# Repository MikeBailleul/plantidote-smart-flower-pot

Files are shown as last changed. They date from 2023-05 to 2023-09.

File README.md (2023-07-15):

# Plantidote - A smart flower pot, self-watering

Plantidote, the antidote to never worry about failing your plants again.

How many times have you found yourself on the brink of dehydration, parched, staring at your glass of water, but too lazy to actually pick it up and sip? Now, imagine that, but you're a plant 🌱. Imagine the thirst. 💦 The despair... 😩

Plantidote will automatically check for moisture level in the planter and will water itself if needed.

# Table of Contents
- [How to build your own](#how-to-build-your-own)
  * [BOM](#bom)
  * [PCB](#pcb)
  * [3D printing](#3d-printing)
- [Build instructions](#build-instructions)
  * [Making the shell water Resistant](#making-the-shell-water-resistant)
  * [Soldering](#soldering)
  * [Assembling the bottom part](#assembling-the-bottom-part)
  * [Assembling the top part](#assembling-the-top-part)
- [Home Assistant & ESPHome Instructions](#home-assistant--esphome-instructions)
- [Blynk Instructions](#blynk-instructions)
- [PCB design choices](#pcb-design-choices)
- [Some Fusion 360 PCB tips](#some-fusion-360-pcb-tips)

# History of the project
Plantidote is based on [this awesome idea](https://github.com/FlauraPlantPot/Flaura) by Martin McMaker.
Unfortunately, it was working only with Blynk and the pot was difficult to make waterproof.

I completely redesigned the PCB and some parts of 3D models.
It is now easier to seal, requiring only 2 seal points. Hot glue or silicone sealant can be used. Thanks to Martin Vinter for [the inspiration](https://github.com/MartinVinter/Flaura2)

This new smart pot works with:
- HomeAssistant/ESPHome. Home Assistant code is derived from MathGaming [modified version of Flaura](https://github.com/mathgaming/FlauraHomeAssistant).  Many thanks to him.
- [Blynk](https://blynk.cloud/)

Plantidote has 4 design variations for the external shell and can be printed in different colors (shell & top lid).

| Round | Knurl | Spin | V Shape |
| --- | --- | --- | --- |
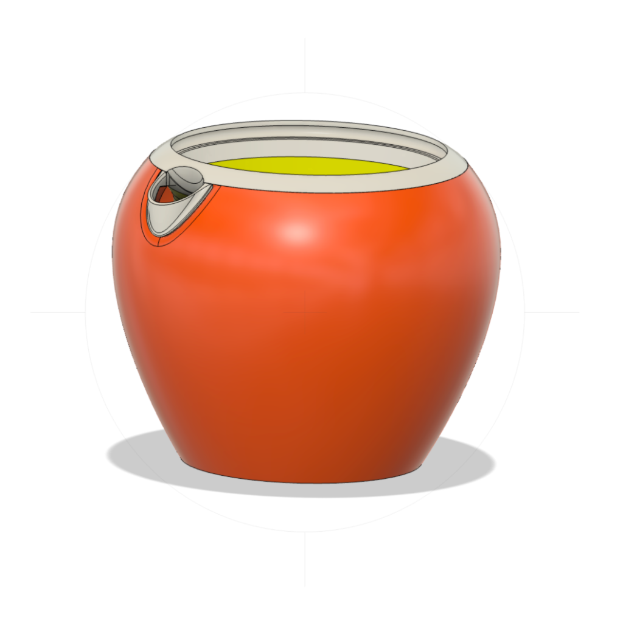
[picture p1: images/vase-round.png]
round
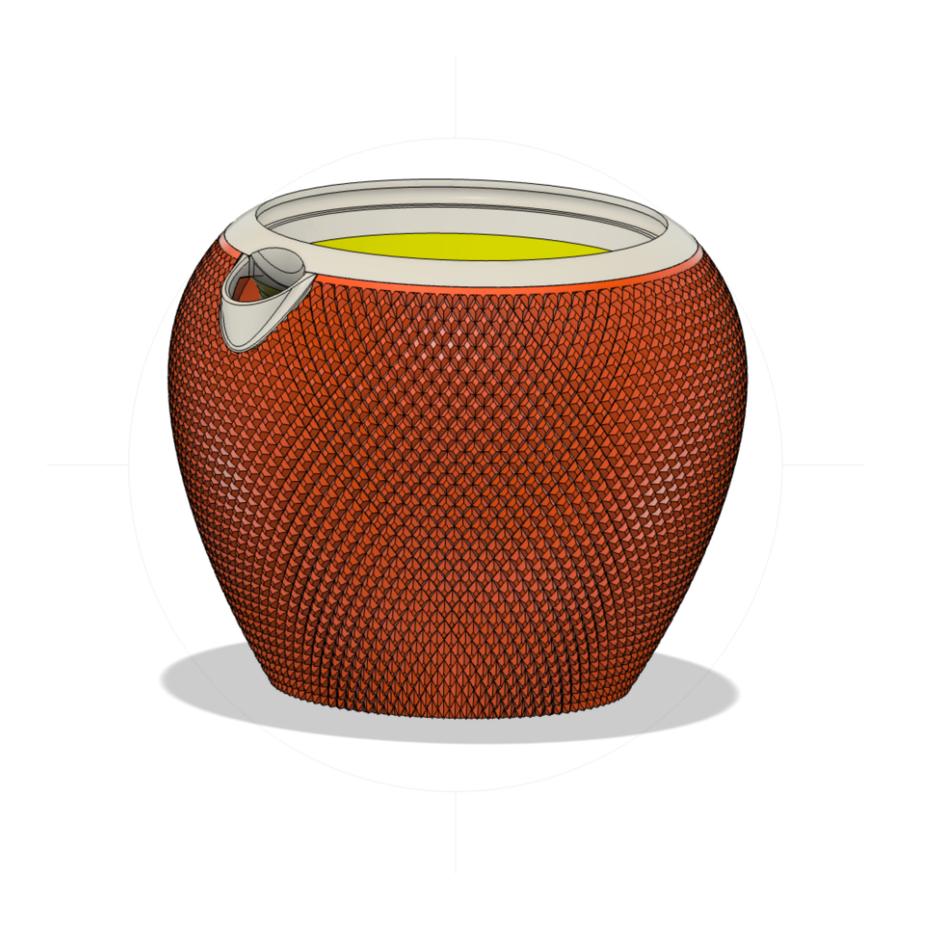
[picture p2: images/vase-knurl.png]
knurl
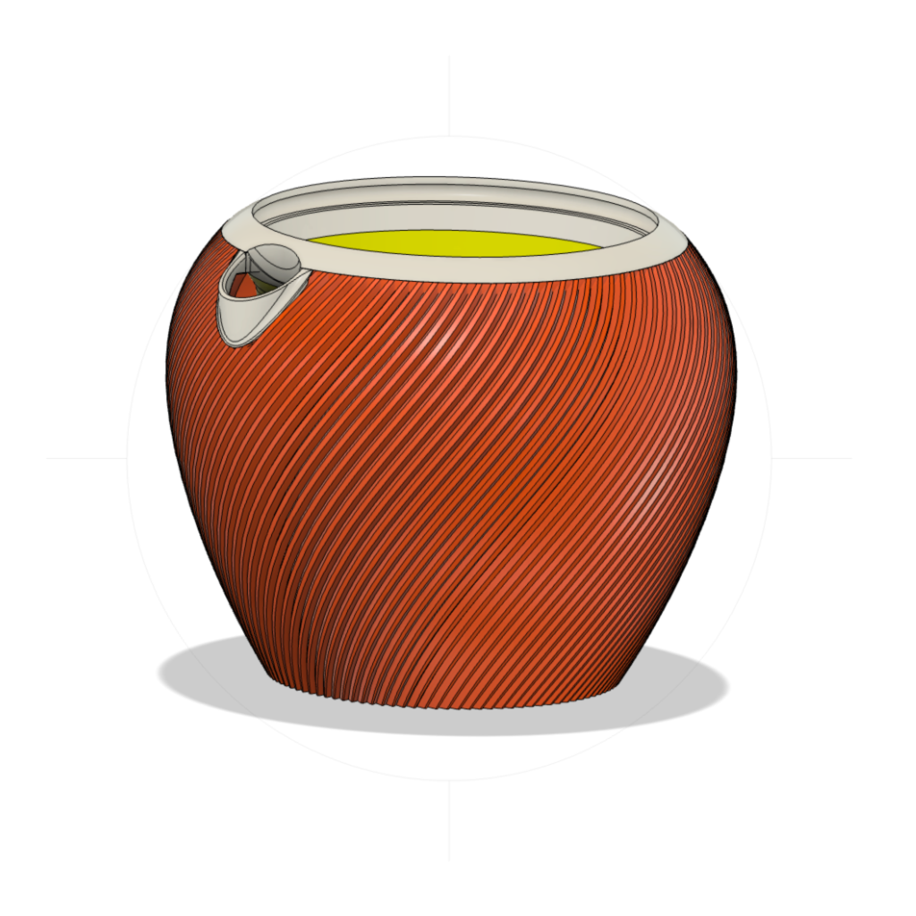
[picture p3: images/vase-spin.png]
spin
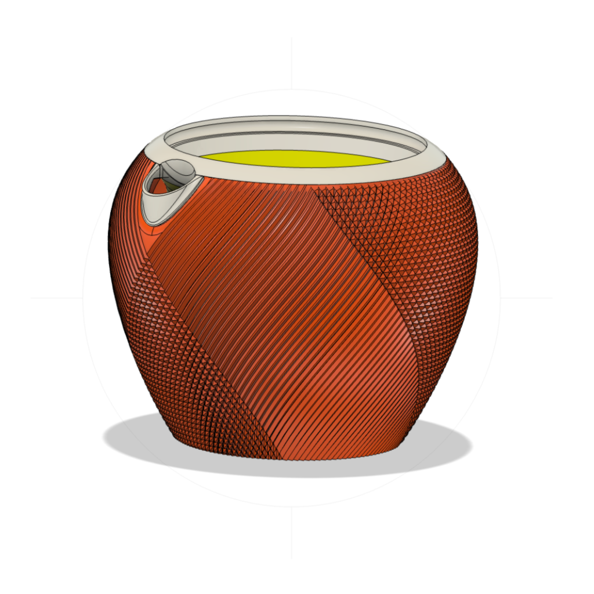
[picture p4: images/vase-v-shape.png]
v shape
|  |  |  |  |

The vase can be autonomous for months thanks to its 0.5L water tank and its battery. The volume of the flower pot is 0.8L.

# How to build your own

## BOM

#### Hoses
| Name | Type | Diameter | Length | Link |
| --- | --- | --- | --- | --- |
| Hose - Watering ring  | PTFE | Ø4-Ø2mm | 365mm | [AliExpress](https://www.aliexpress.com/item/1005001976975889.html) |
| Hose - Ring/T | Silicone | Ø5-Ø3mm | 90mm | [AliExpress](https://www.aliexpress.com/item/1005002185082384.html) |
| Hose - "bridge" T-connector/Pot | Silicone | Ø5-Ø3mm | 2 x 15mm | [AliExpress](https://www.aliexpress.com/item/1005002185082384.html) |
| Hose - Pump | Silicone | Ø5-Ø3mm | 40mm + 50mm | [AliExpress](https://www.aliexpress.com/item/1005002185082384.html) |
| T-connector |  | Ø3.2-Ø2.4mm |  | [AliExpress](https://www.aliexpress.com/item/1005004196182380.html) |

PVC hose could work as well, but I advise silicone instead because it is softer and will prevent you from breaking the 3D printed hose connectors.

#### Electronics
| Quantity | Name | Specs | Note | Link |
| --- | --- | --- | --- | --- |
| 1 | Lolin D32 |  |  | [AliExpress](https://www.aliexpress.com/item/32808551116.html) |
| 1 | Diaphragm water pump | DC 3.7V | 2 visible diaphragms -> suitable for water | [AliExpress](https://www.aliexpress.com/item/4000974989453.html) |
| 3 | Resistor | 100kΩ |  | [AliExpress](https://www.aliexpress.com/item/32636020144.html) |
| 1 | Resistor | 330Ω |  | [AliExpress](https://www.aliexpress.com/item/32636020144.html) |
| 1 | Ceramic capacitor | 100nF |  | [AliExpress](https://www.aliexpress.com/item/1005003563792431.html) |
| 1 | Diode 1N4007 | 1A |  | [AliExpress](https://www.aliexpress.com/item/32633071171.html) |
| 1 | MOSFET IR**L**Z44N | Logic level | Don't confuse with : IR**F**Z44N | [AliExpress](https://www.aliexpress.com/item/32714396199.html) |
| 1 | Push button | 6x6x4.3mm |  | [AliExpress](https://www.aliexpress.com/item/4001223843274.html) |
| 1 | Power switch | SK12D07VG6 (6mm) |  | [AliExpress](https://www.aliexpress.com/item/1005003663462833.html) |
| 2 | Pin Header Female 16 Pins |  | PCB/LolinD32 connectors | [AliExpress](https://www.aliexpress.com/item/33004522737.html) |
| 1 | Pin Header Male 3 Pins |  | PCB/Moisture sensor connectors | [AliExpress](https://www.aliexpress.com/item/32758380907.html) |
| 2 | JST Connector Male/Female 2 Pins | PH Pitch 2.0 | Pump & battery connectors | [AliExpress](https://www.aliexpress.com/item/33009614944.html) 
| 1 | JST Connector Male/Female 5 Pins + cables  | PH Pitch 2.0 | Water level sensor connector | [AliExpress](https://www.aliexpress.com/item/1005001782972538.html) |
| 1 | 18650 Li-Ion Battery Cylindrical 2200mAh 3.7V **with JST Connector** | 3.7V, > 2000 mAh, Protection circuitry included | I strongly discourage to buy cheap batteries on AliExpress, buy good batteries = safer and less issues | [AdaFruit](https://www.adafruit.com/product/1781) |
| 1 | Capacitive Soil Moisture Sensor |  | I strongly encourage you to watch [this video](https://www.youtube.com/watch?v=IGP38bz-K48) to avoid sensor issues | [AliExpress](https://www.aliexpress.com/item/32832538686.html) |
| 1 | Type-C Adapter USB C to Micro USB |  | Optional | [AliExpress](https://www.aliexpress.com/item/33035034558.html) |

#### Others
| Quantity | Name | Specs | Note | Link |
| --- | --- | --- | --- | --- |
| 4 | M3x6 screw |  | PCB screws | [AliExpress](https://www.aliexpress.com/item/1005005469135111.html) |
| 4 | M3x8 screw |  | Pump and battery screws | [AliExpress](https://www.aliexpress.com/item/1005005469135111.html) |
| 1 | Silicone rubber glue sealant |  | | [AliExpress](https://www.aliexpress.com/item/1005002041941459.html) |

## PCB
The easiest way would be to order the custom PCB via this [affiliate link](https://www.pcbway.com/project/shareproject/Plantidote_0ff0f20b.html).
Alternatively, you can use the gerber files in this repo and send them to your manufacturer of choice.

| 2D | Schematics |
| --- | --- |
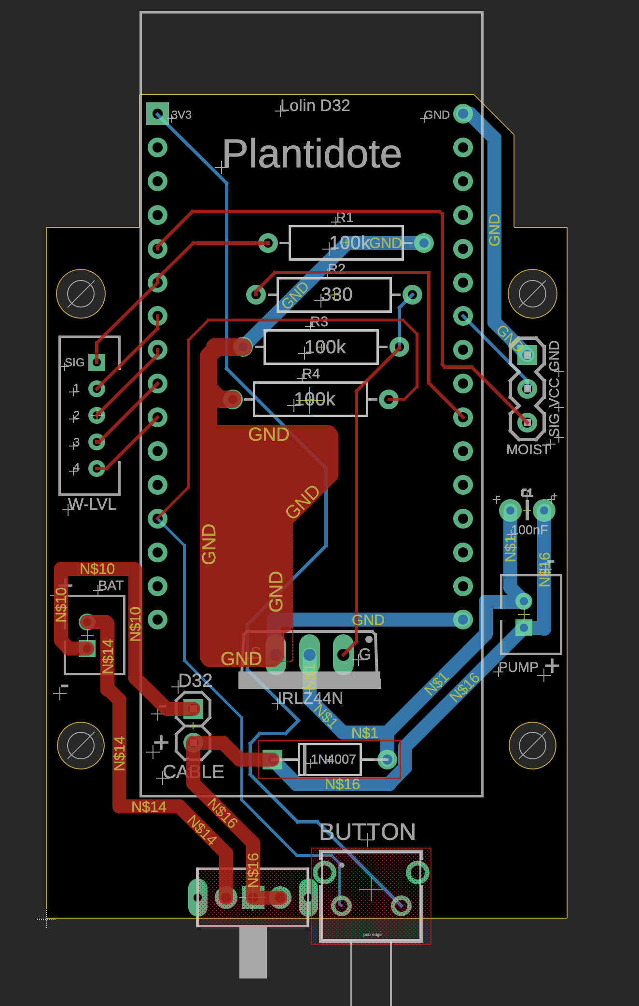
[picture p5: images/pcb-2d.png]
2d
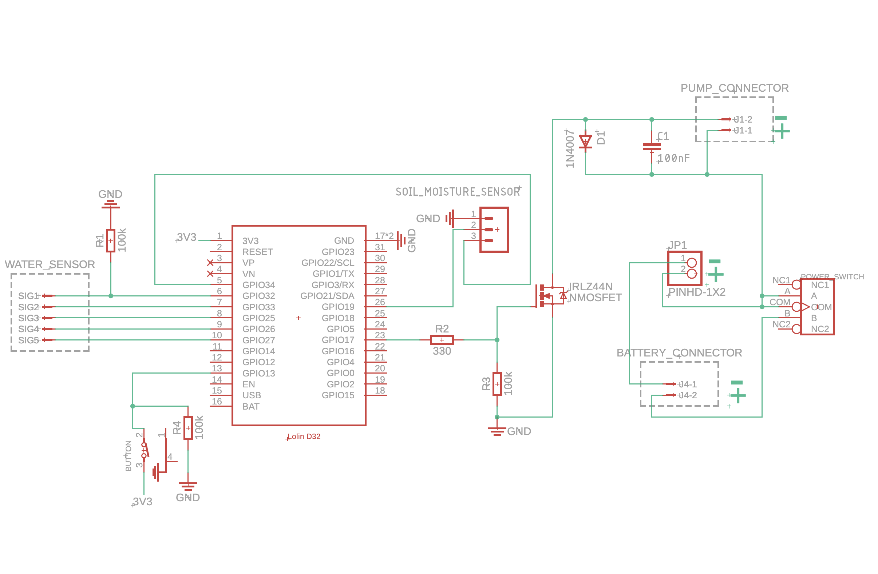
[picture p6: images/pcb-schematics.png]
schematics
|  |  |

## 3D printing

### Print parts
Choose one of the shell variations. Print time is indicated below.

| Round: 1j13h | Knurl: 3j5h | Spin: 3j5h | V Shape: 3j3h |
| --- | --- | --- | --- |
| round | knurl | spin | v shape |

Mandatory print parts:

- shell of your choice
- top lid
- inner planter
- battery holder
- pump holder
- sensor holder

Optional print parts:

- water sensor cable tester -> will help you determine the length of the cable needed
- sensor protector -> will help you protect the roots of the plants when filling the inner planter

### Print settings
You can print in PLA or PETG, both worked fine for me.

The simplest way is to use the .3mf file and print them directly with PrusaSlicer, it's already all configured.

In case you need to set the settings yourself for the shells, here they are:

- print on it's head
- 0.15mm layer with 0.4mm nozzle
- layers & perimeters
	- vertical shells -> perimeters: 7
	- horizontal shell -> solid layers > top: 15
	- enable external perimeters first
	- seam: rear
- infill
	- density: 90%
	- bridging angle: 55
- supports
	- support style: snug
	- bottom contaxt Z distance: 0.1
	- bottom interface layer: 1
- speed
	- bridges: 15mm/s
	- first layer: 15mm/s
- custom range 4-13mm
	- speed -> bridge: 8mm/s

## Build instructions

### Making the shell water resistant

**1.** place the moisture sensor in its hole. **IMPORTANT**: if you haven't watched [that video about fixing moisture sensors issues](https://www.youtube.com/watch?v=IGP38bz-K48) yet, now is the time before you proceed with sealing the moisture sensor
<br />**2.** secure the moisture sensor with the sensor holder
<br />**3.** seal it with the silicone glue on the inner part
<br />**4.** seal it with the silicone glue on the bottom part

| 1 | 2 | 3 | 4 |
| --- | --- | --- | --- |
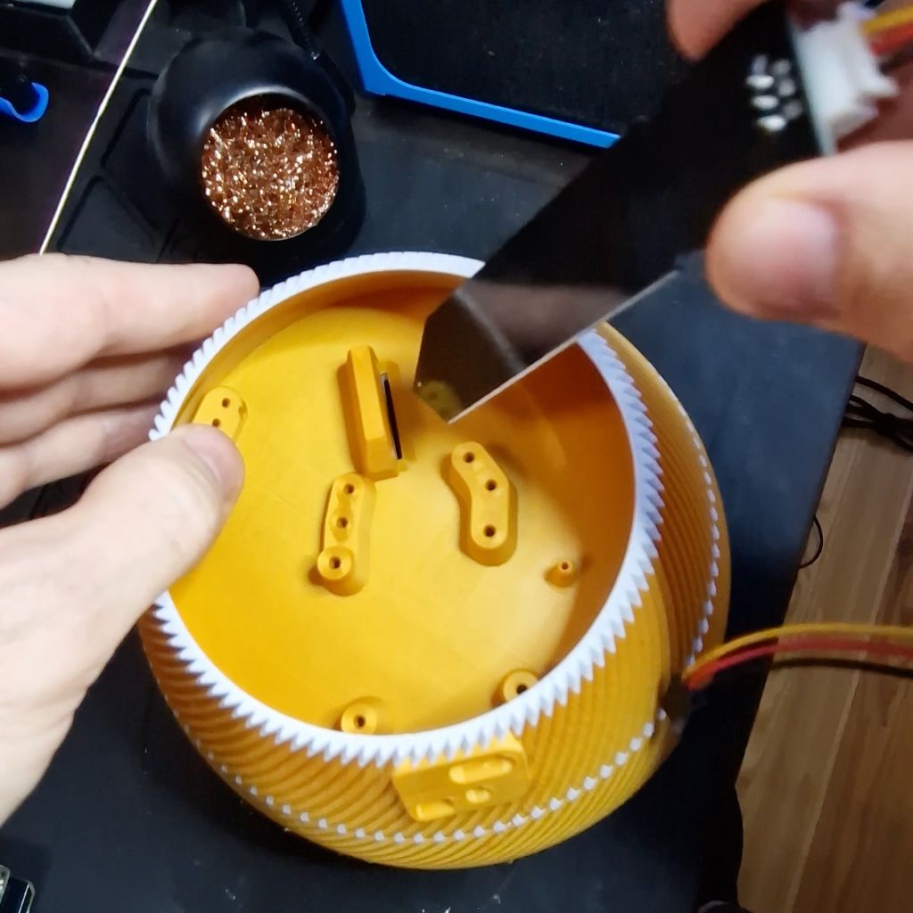
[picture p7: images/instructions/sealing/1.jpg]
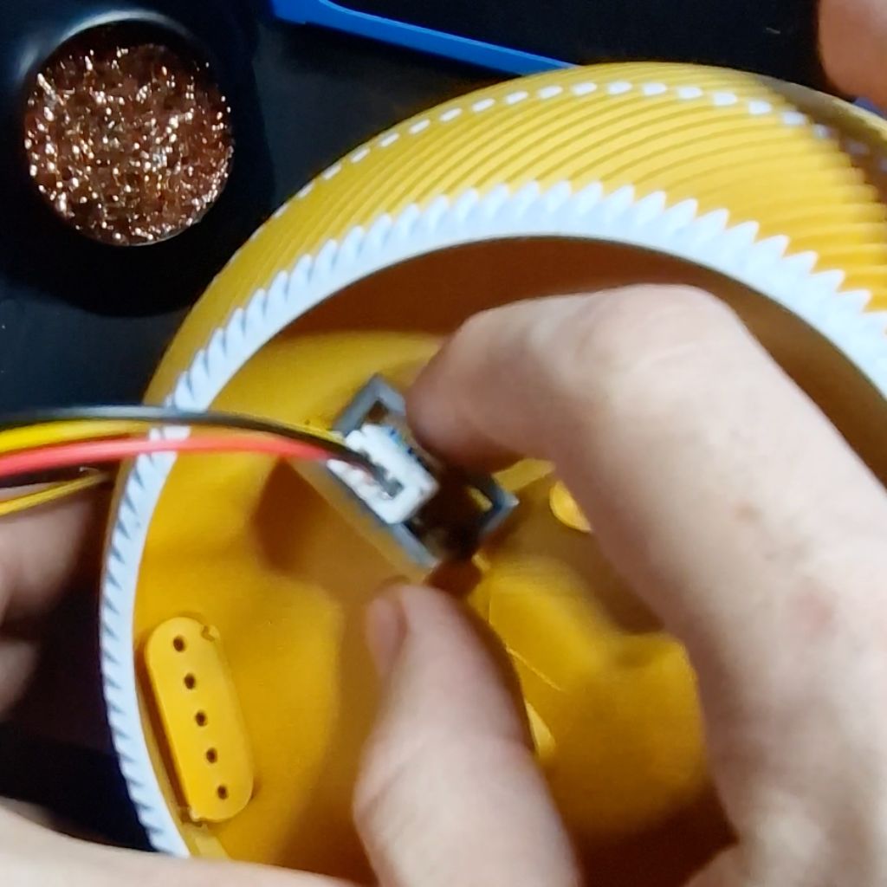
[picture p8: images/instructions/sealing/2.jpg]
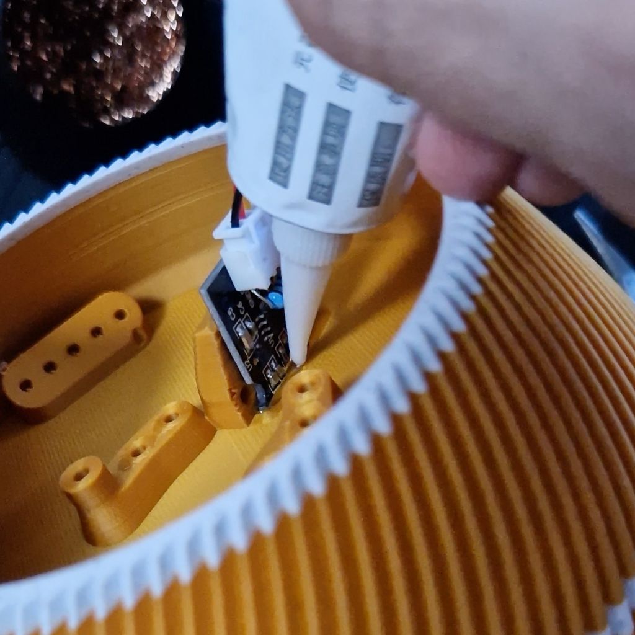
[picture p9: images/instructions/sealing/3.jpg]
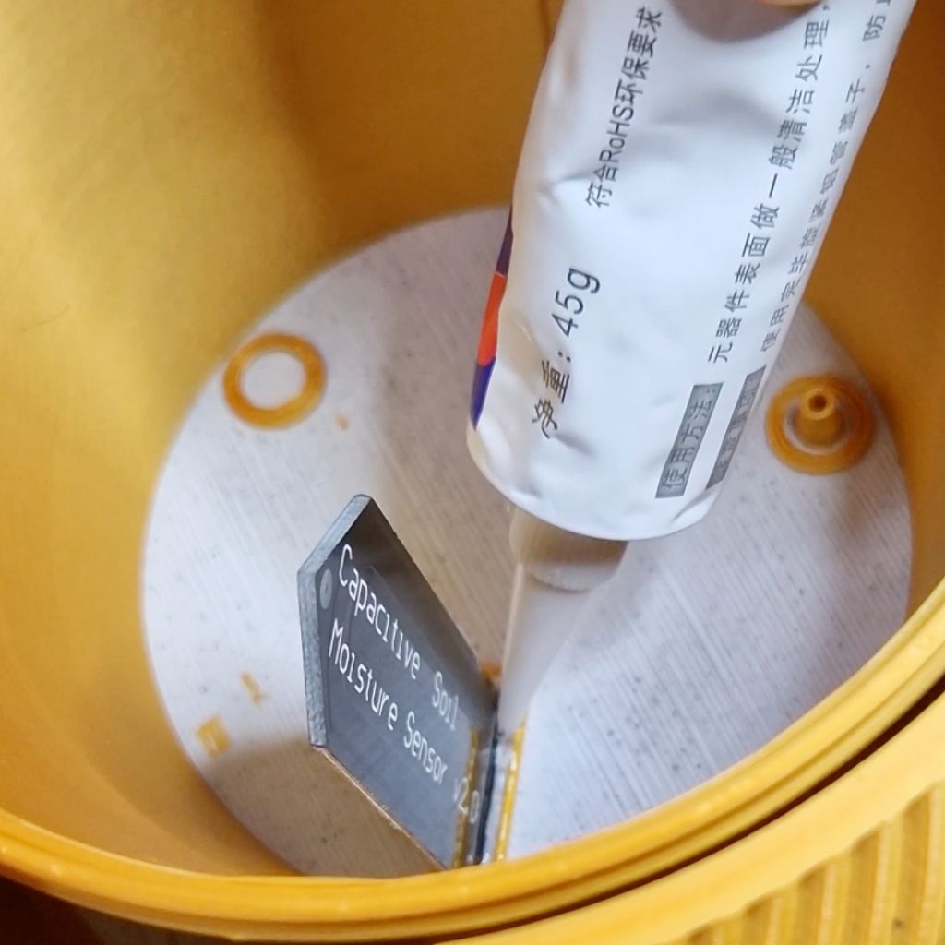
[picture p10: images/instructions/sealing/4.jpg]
|  |  |  |  |

<br />**5.** optional: apply silicone in the inner part of the vase as shown by the red circle. I'ts optional because it will depend on your print and filament quality.
<br />**6.** use the 5 pins cable and insert them into the "water sensor cable tester" as shown on the picture. Then mark the limit with a pen
<br />**7.** insert those 5 pins cable into the vase until you reach the mark (ground is indicated by a small cut next to the hole)
<br />**8.** seal it with the silicone glue
<br />**9.** **wait 48h** for it to dry
<br />**10.** put a silicone hose between the 2 bottom connectors and pour water into the tank to test for leakage (if needed, fix them with silicone glue)

| 5 | 6 | 7 |
| --- | --- | --- |
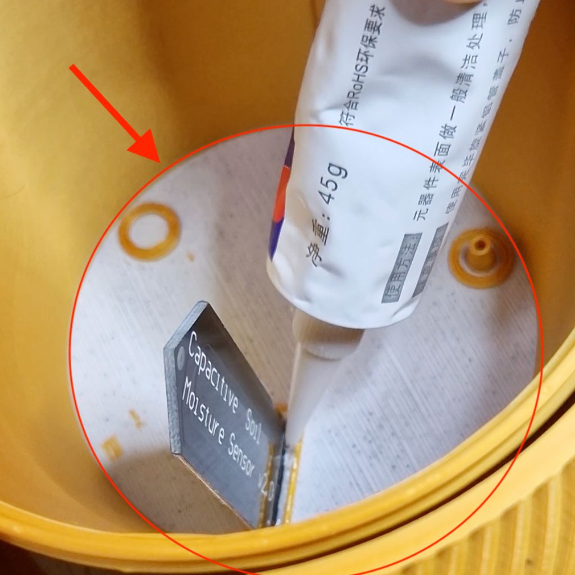
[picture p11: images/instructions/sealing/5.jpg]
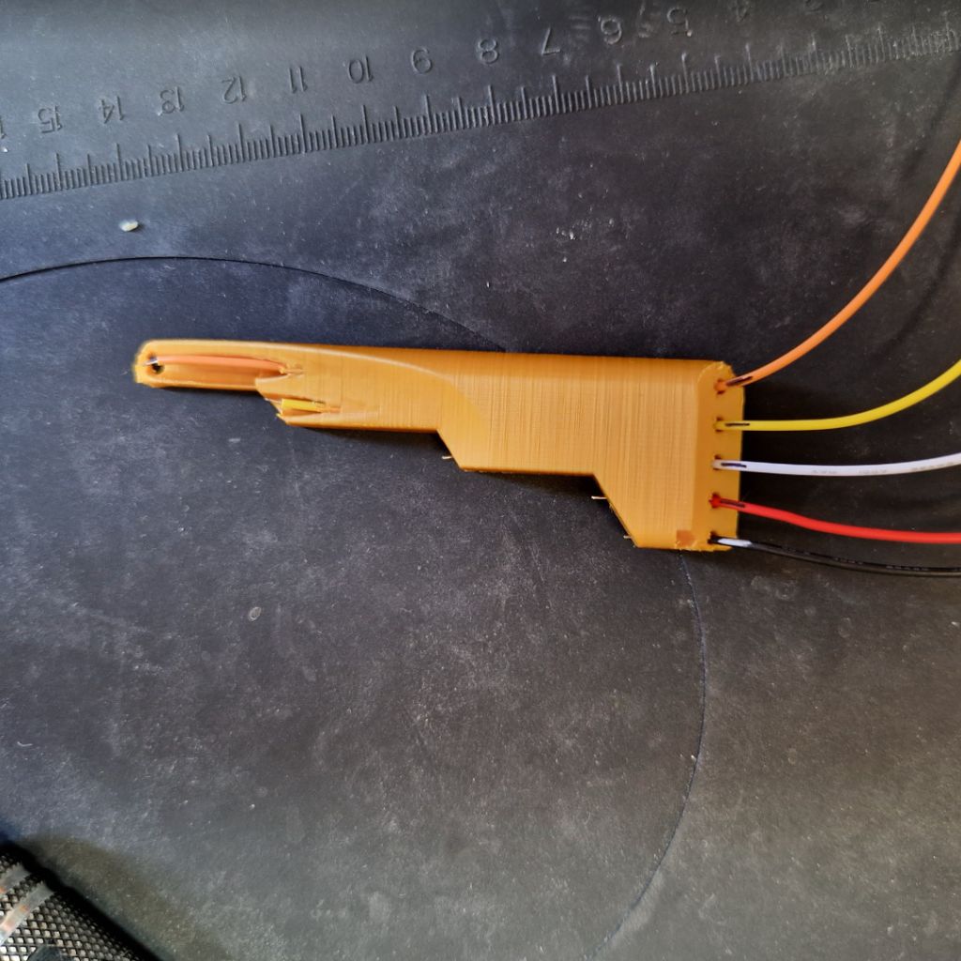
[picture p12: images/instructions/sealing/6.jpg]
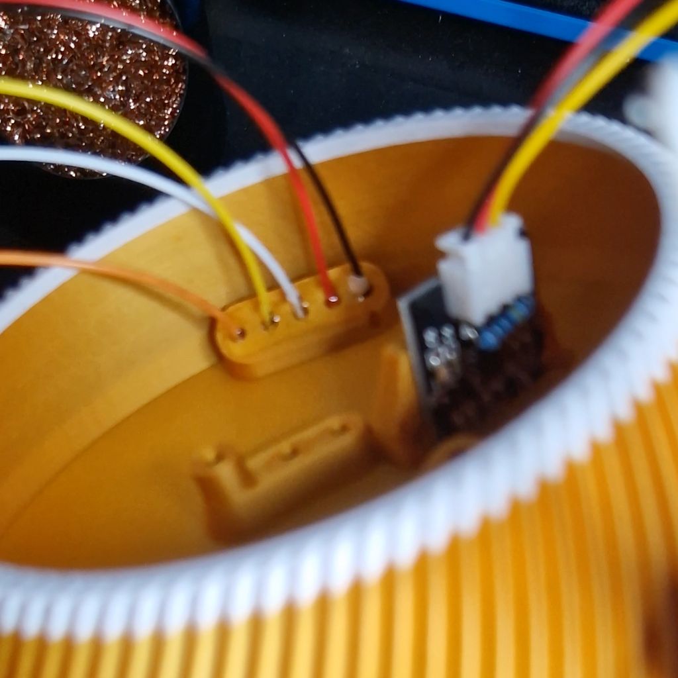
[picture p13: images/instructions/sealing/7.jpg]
|  |  |  |

### Soldering
It should not be hard to know what goes where since it is very well indicated on the PCB.<br />
<br />**1.** everything has to be soldered from the back of the PCB
<br />**2.** solder the 16 pins male to the PCB
<br />**3.** solder the 4 resistors and the ceramic capacitor

| 1 | 2 | 3 |
| --- | --- | --- |
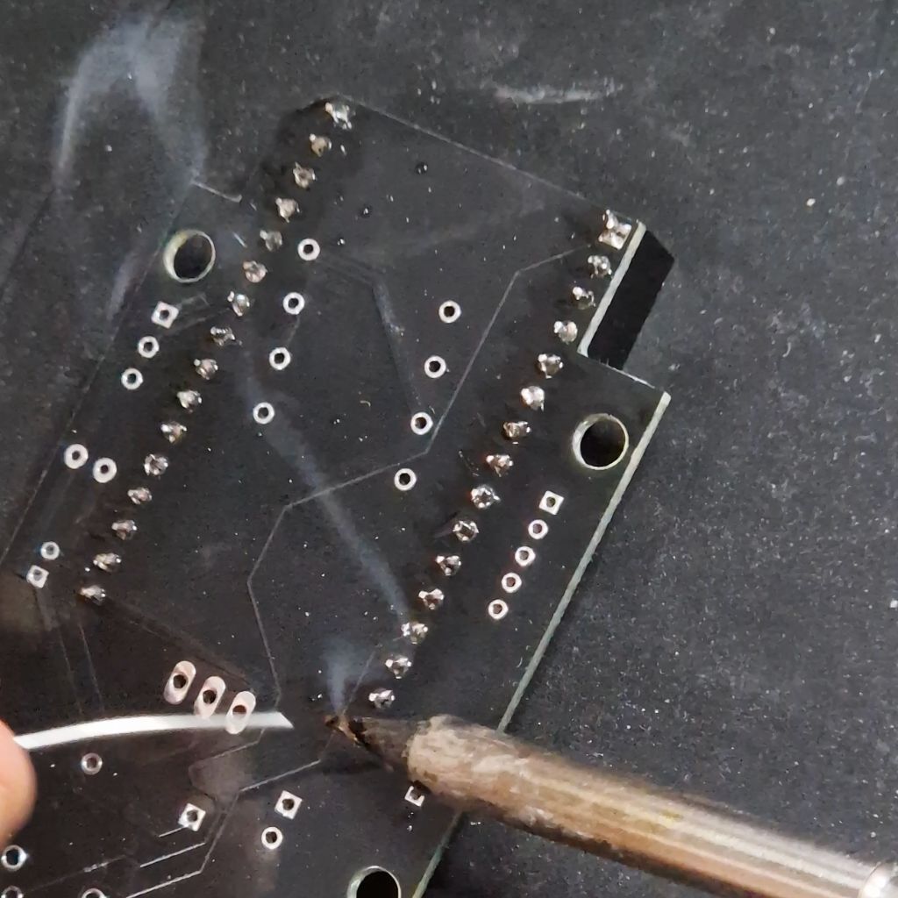
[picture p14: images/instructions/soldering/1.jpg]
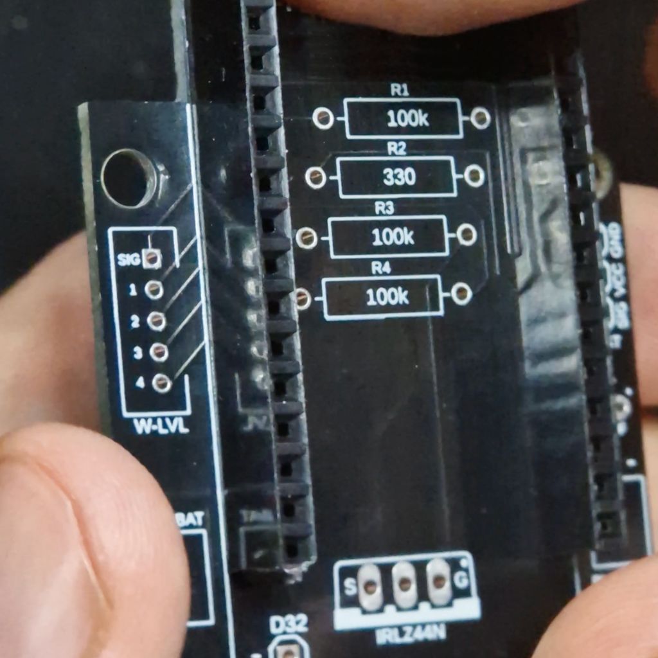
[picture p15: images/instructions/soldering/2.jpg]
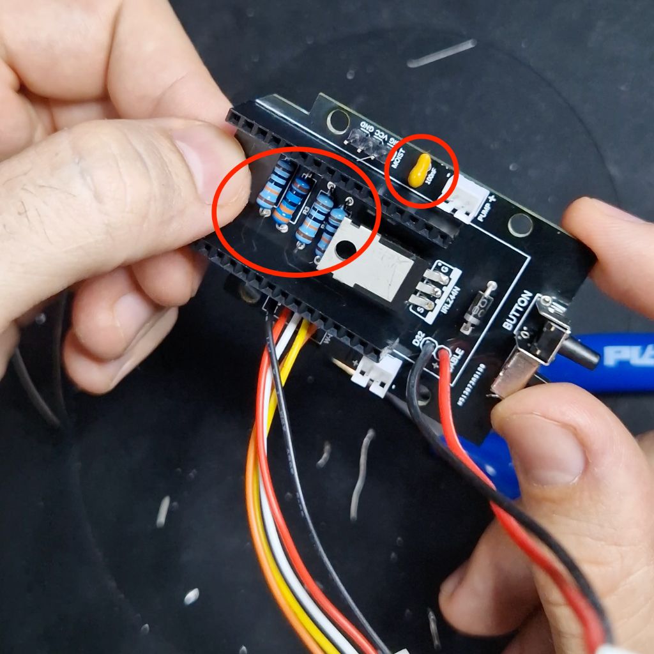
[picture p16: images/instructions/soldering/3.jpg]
|  |  |  |

<br />**4.** solder the diode and the MOSFET, **be very careful, the left/right side of these components matters**
<br />**5.** solder JST connectors for the pump and the battery, **be very careful, there is no standard on JST connectors**, the pins could be inverted for your connectors. Check that your red cable for the pump is on the "+" side of the board and black cable on the "-". Do the same for the battery connector. **Failure to check that could destroy your compotents**.
<br />**6.** solder the button and the power switch 

| 4 | 5 | 6 |
| --- | --- | --- |
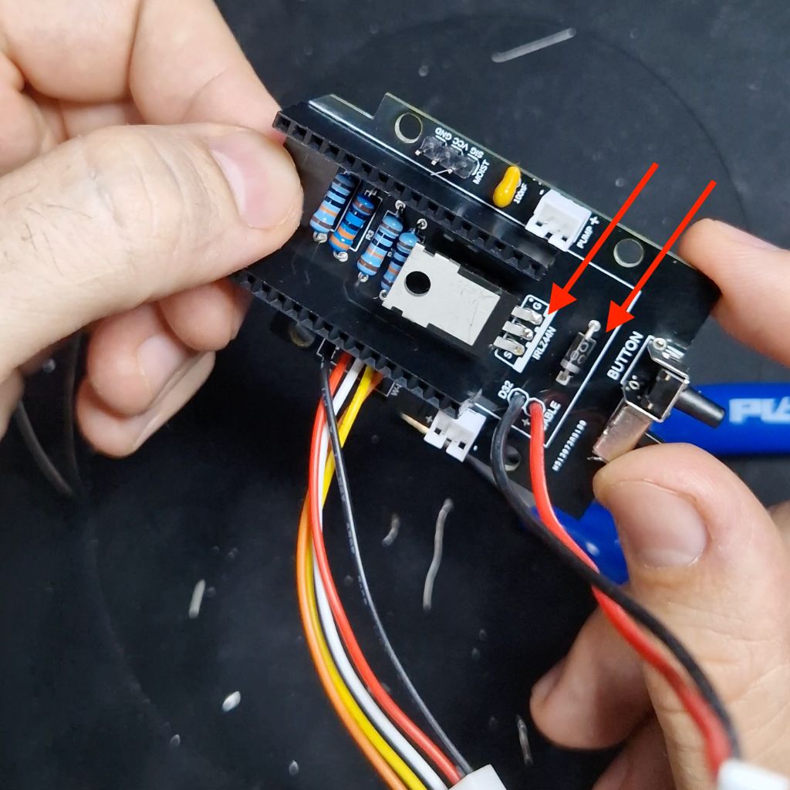
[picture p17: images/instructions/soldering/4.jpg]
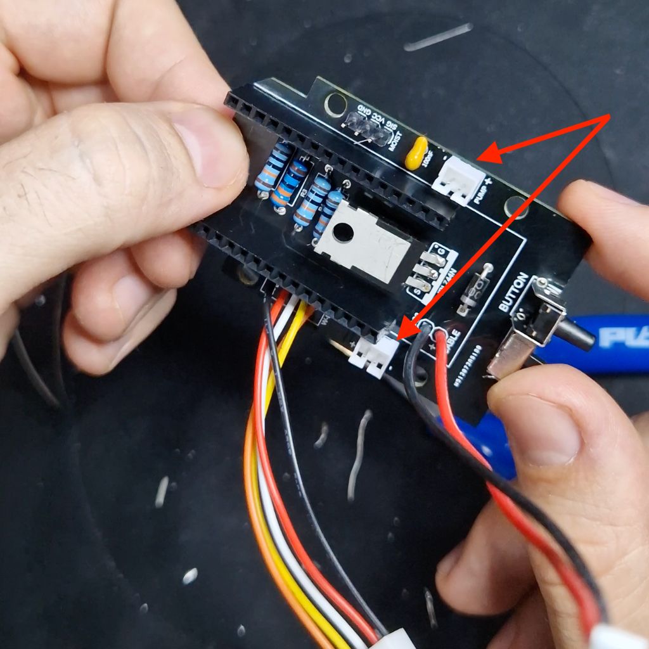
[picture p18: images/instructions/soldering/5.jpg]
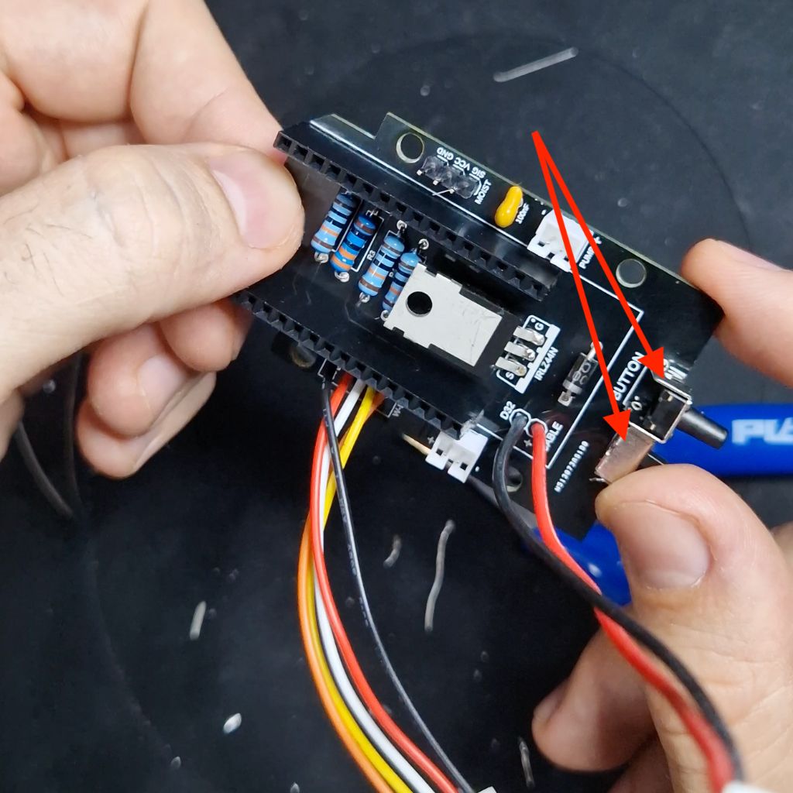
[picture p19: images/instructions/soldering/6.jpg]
|  |  |  |

<br />**7.** solder the 3 pins moisture sensor and the 5 pins connector (on the picture, you can see I use 5 cables intead of a 5 pins connectors but it is exactly the same)
<br />**8.** solder 1 cable with JST connector to the battery pins on the PCB 
<br />**9.** attach the LolinD32 to the PCB and plug the battery cable

| 7 | 8 | 9 |
| --- | --- | --- |
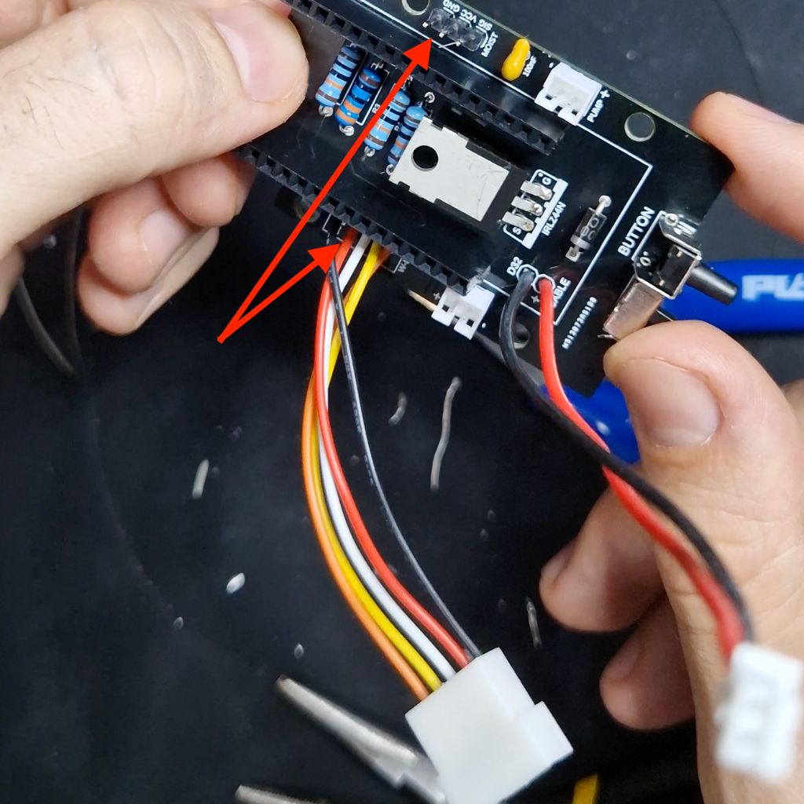
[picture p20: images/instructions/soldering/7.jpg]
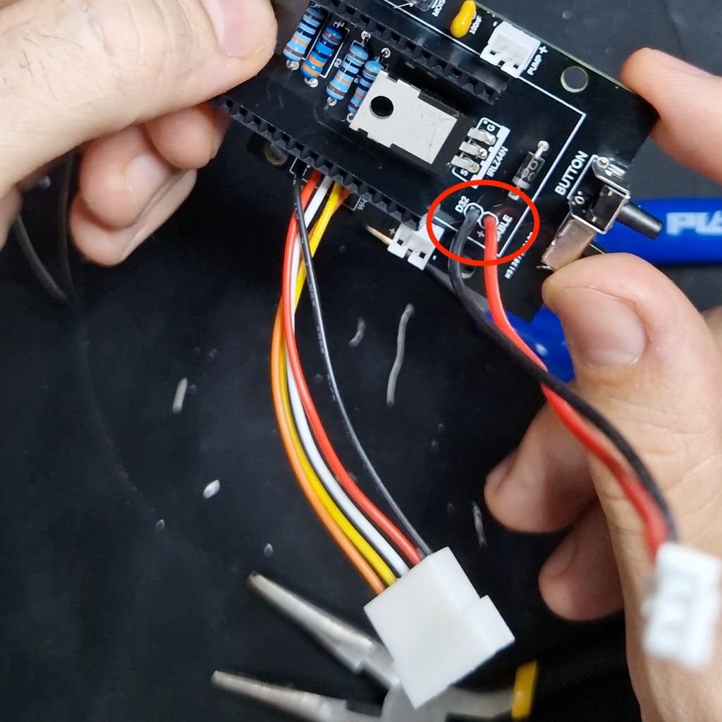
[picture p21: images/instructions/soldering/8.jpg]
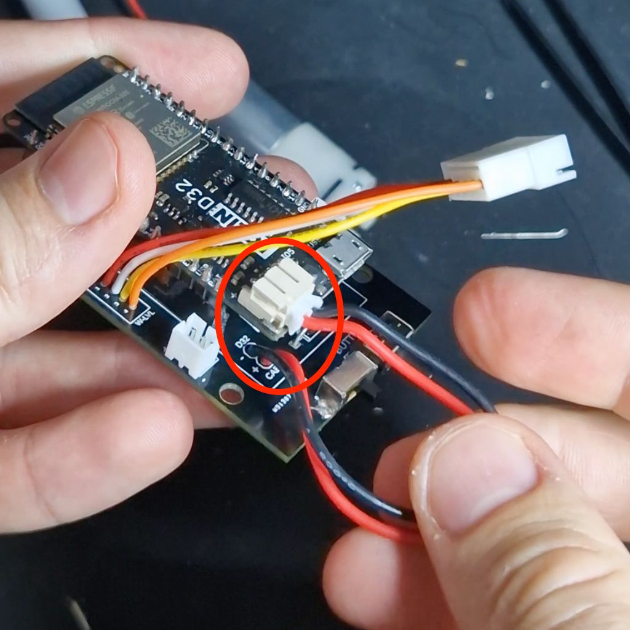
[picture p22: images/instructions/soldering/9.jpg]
|  |  |  |

### Assembling the bottom part 

**1.** install the battery + holder using two M3x8 screws
<br />**2.** cut 40mm and 50mm from the Ø5-Ø3mm hose, connect them to the pump and the hose connectors. If you bought the exact same pump as I did, the bigger connector on the pump is pushing out water, connect this one to the inner connector.
<br />**3.** install the pump + holder using two M3x8 screws
<br />**4.** install the PCB with two M3x6 screws

| 1 | 2 | 3 | 4 |
| --- | --- | --- | --- |
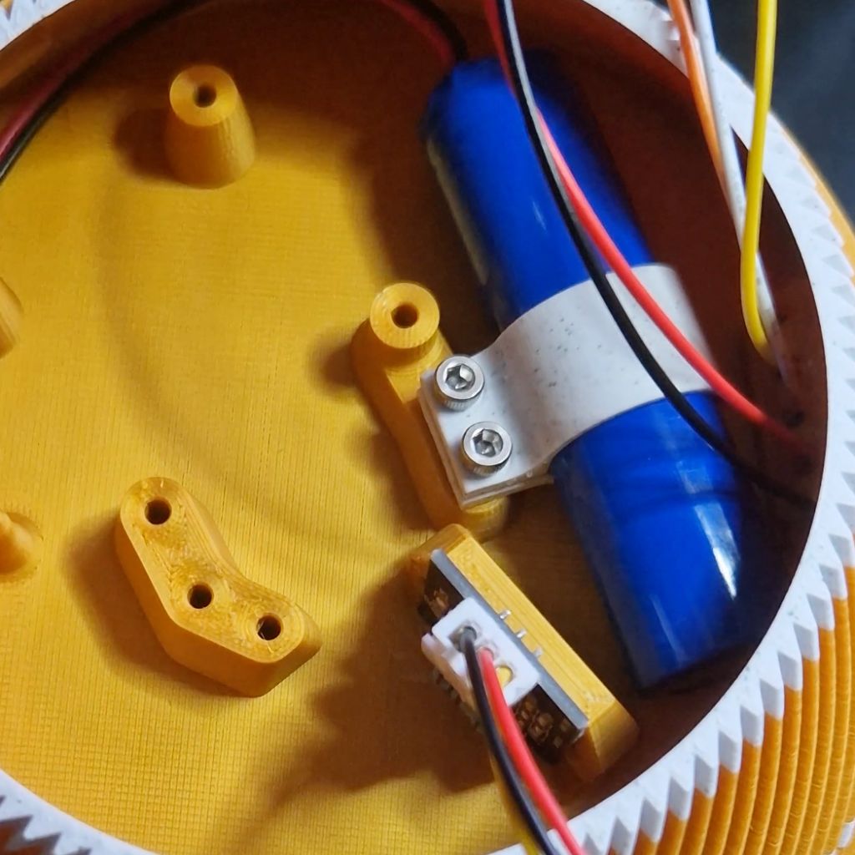
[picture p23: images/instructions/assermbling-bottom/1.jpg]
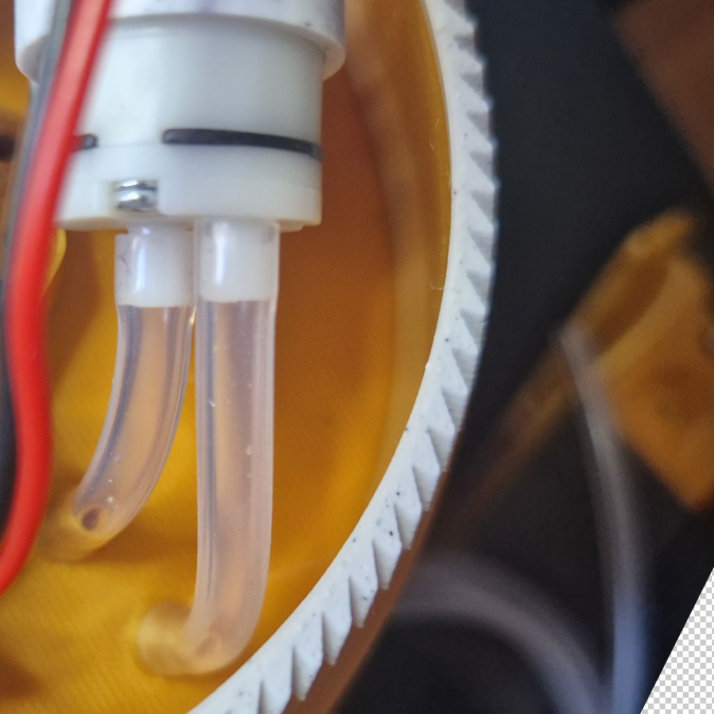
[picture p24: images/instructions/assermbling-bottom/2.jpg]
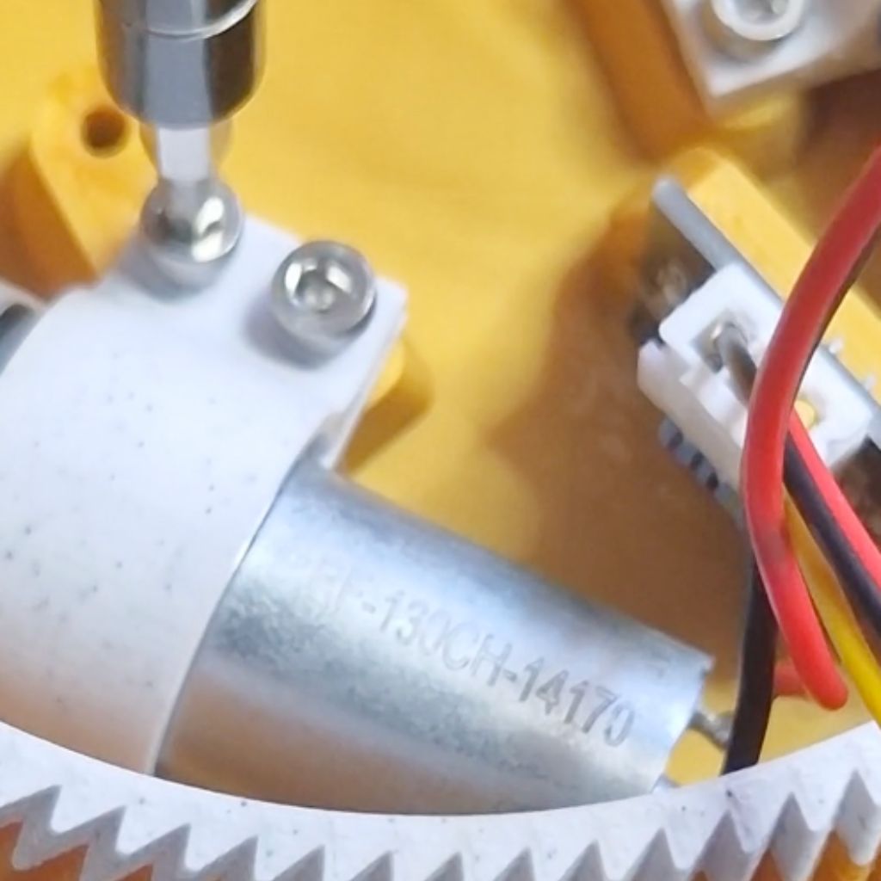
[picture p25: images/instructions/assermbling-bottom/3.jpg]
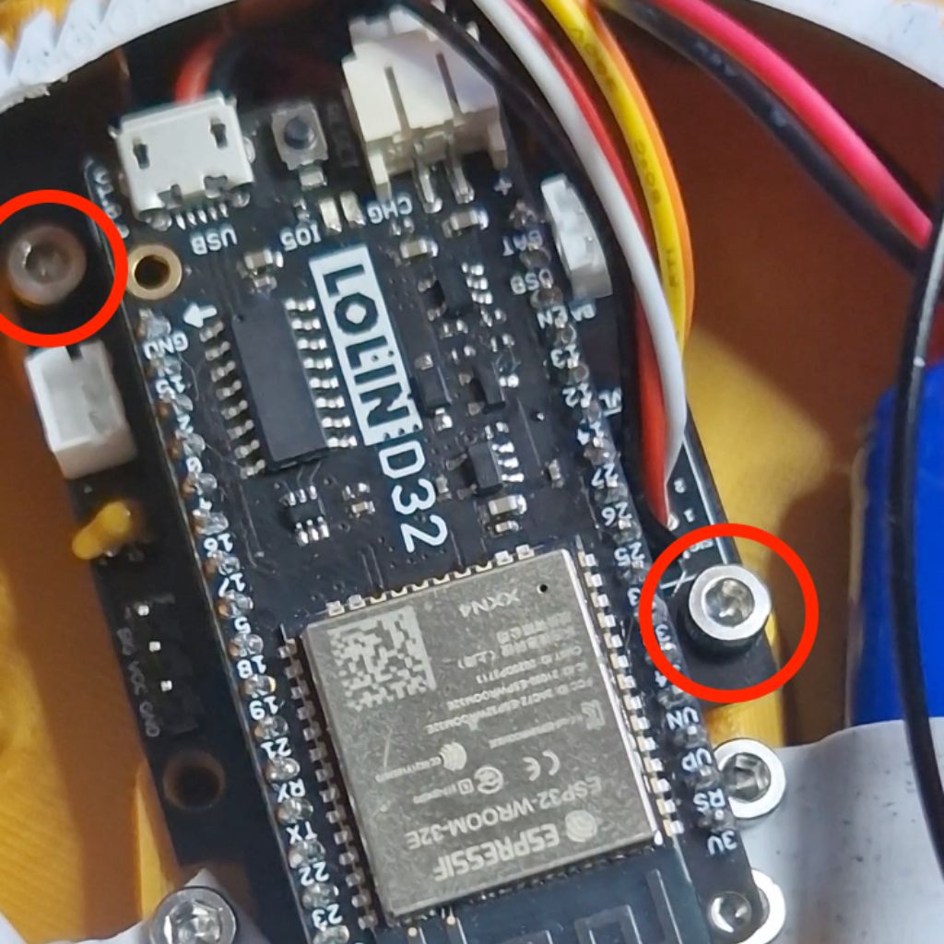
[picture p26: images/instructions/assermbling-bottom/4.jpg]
|  |  |  |  |
	
<br />**5.** plug all cables to their to their connectors
<br />**6.** plug the USB C adapter

| 5 | 6 |
| --- | --- |
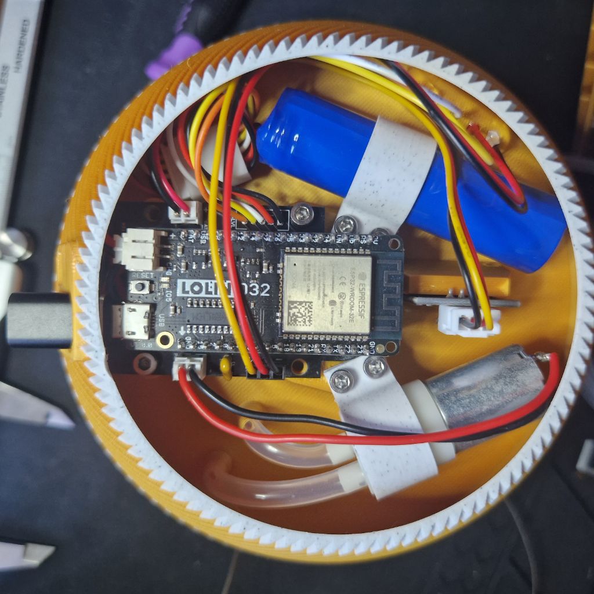
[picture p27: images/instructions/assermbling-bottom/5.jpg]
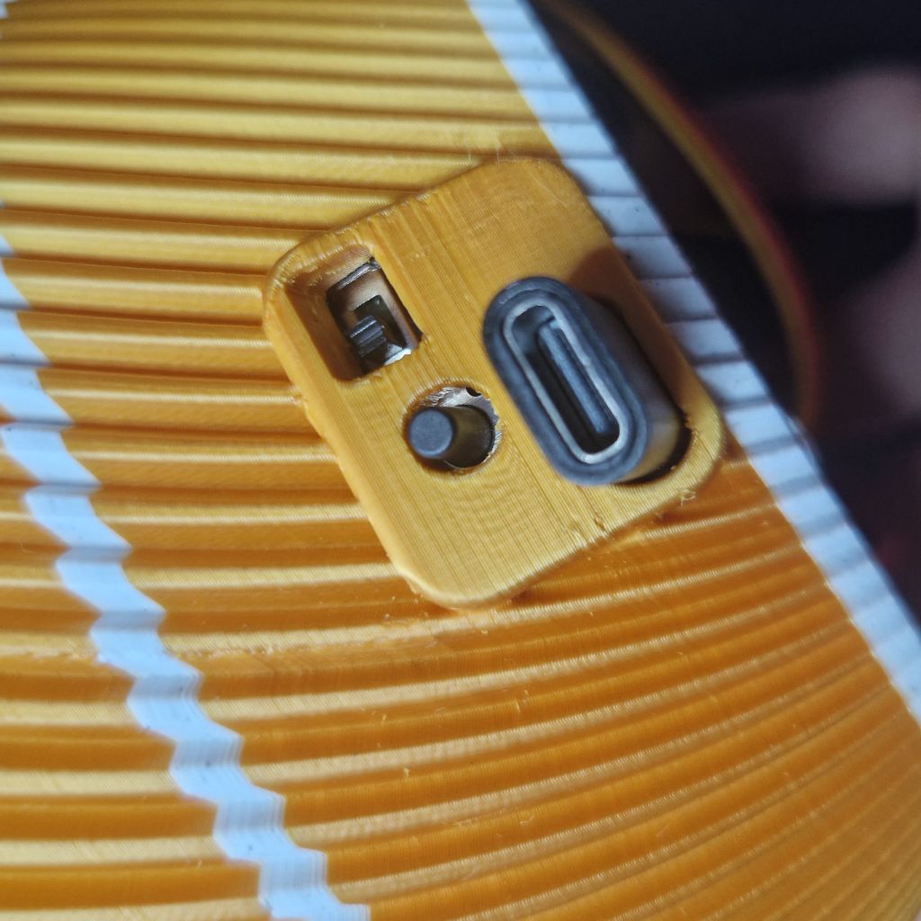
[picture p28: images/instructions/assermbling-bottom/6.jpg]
|  |  |

### Assembling the top part

**1.** cut 15mm from the Ø5-Ø3mm hose **twice**
<br />**2.** connect them to the T-connector
<br />**3.** cut 365mm of the the Ø4-Ø2mm hose
<br />**4.** connect it with the T-connector

| 1 | 2 | 3 | 4 |
| --- | --- | --- | --- |
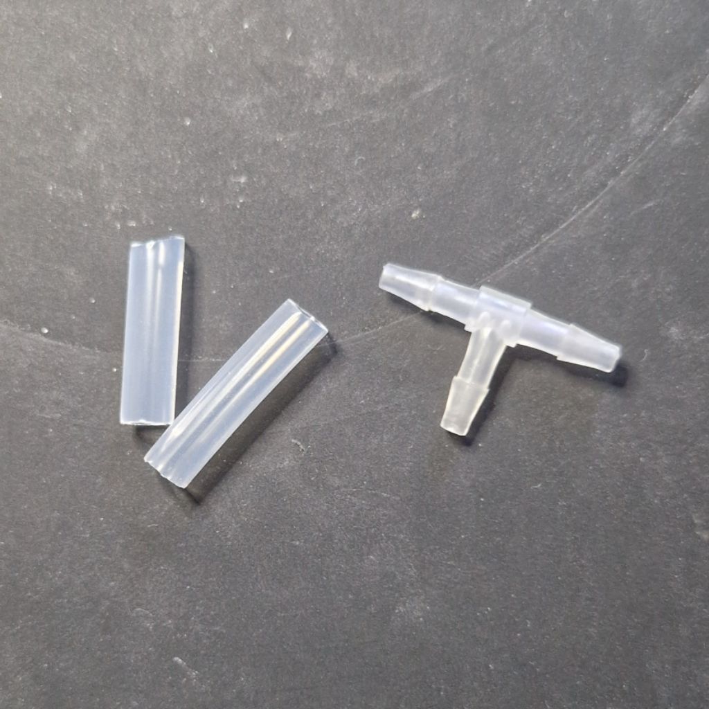
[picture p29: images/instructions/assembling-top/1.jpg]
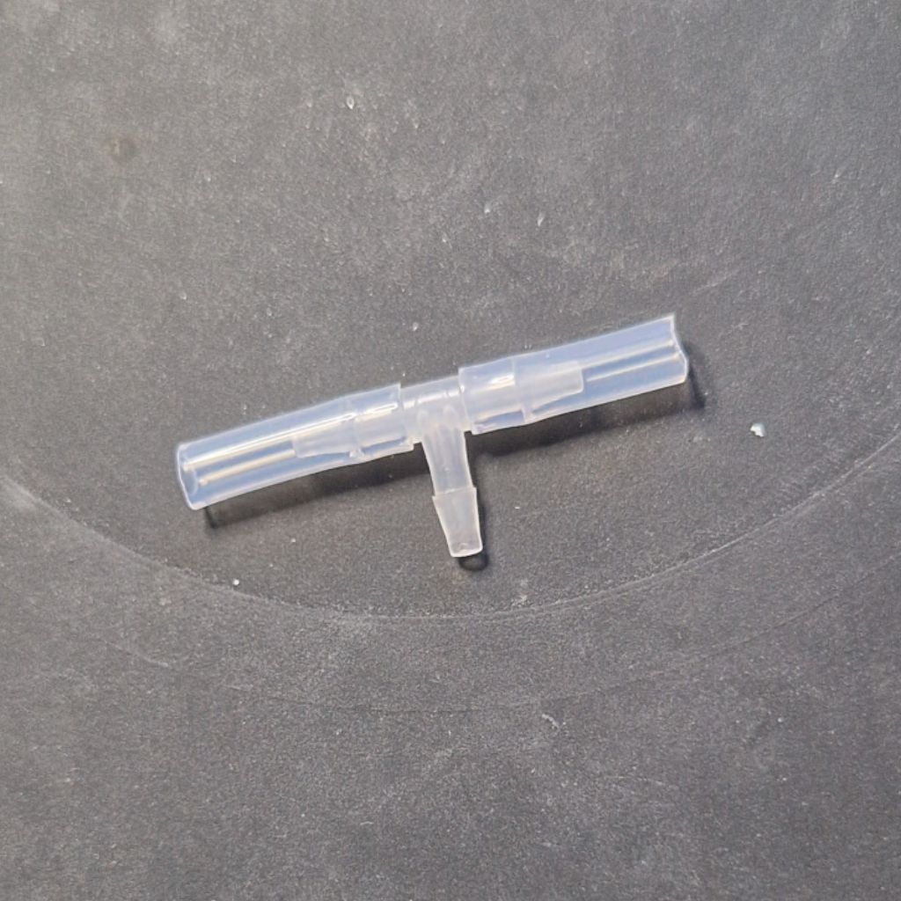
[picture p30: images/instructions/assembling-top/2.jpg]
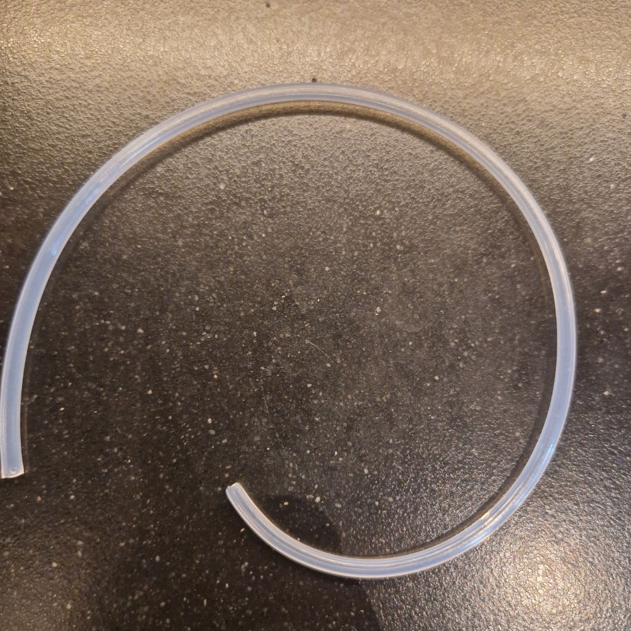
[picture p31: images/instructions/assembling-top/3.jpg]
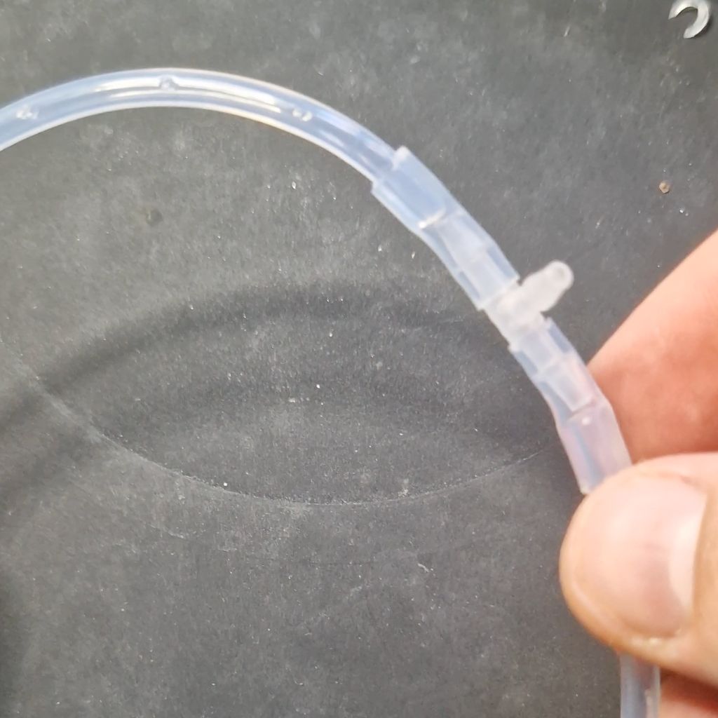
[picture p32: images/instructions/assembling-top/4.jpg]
|  |  |  |  |

<br />**5.** put the ring into the lid
<br />**6.** use a sharp tool to create small watering holes (8 to 12 worked for me)
<br />**7.** place the lid onto the vase, it should easily fit in and out
<br />**8.** cut 90mm from the the Ø5-Ø3mm hose and connect it to the bottom of the pot and the T-connector

| 5 | 6 | 7 | 8 |
| --- | --- | --- | --- |
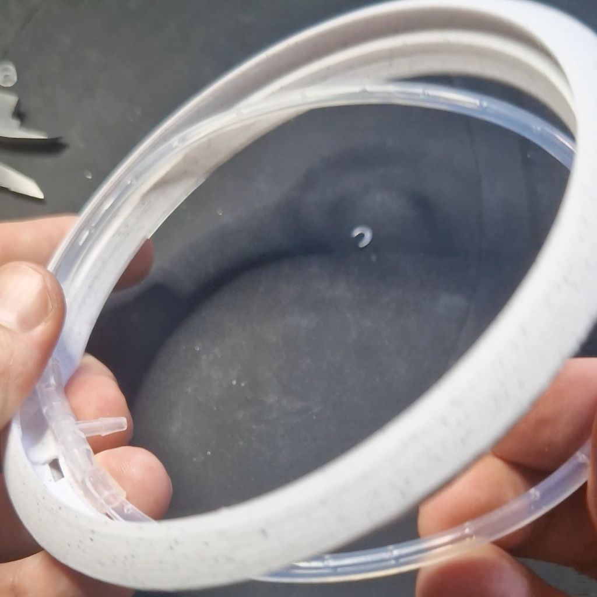
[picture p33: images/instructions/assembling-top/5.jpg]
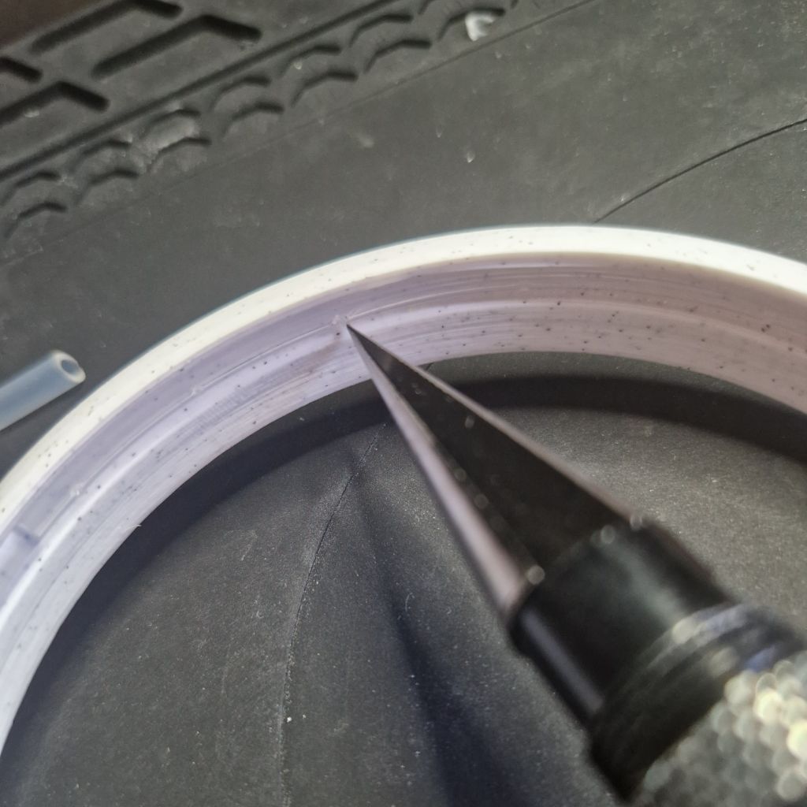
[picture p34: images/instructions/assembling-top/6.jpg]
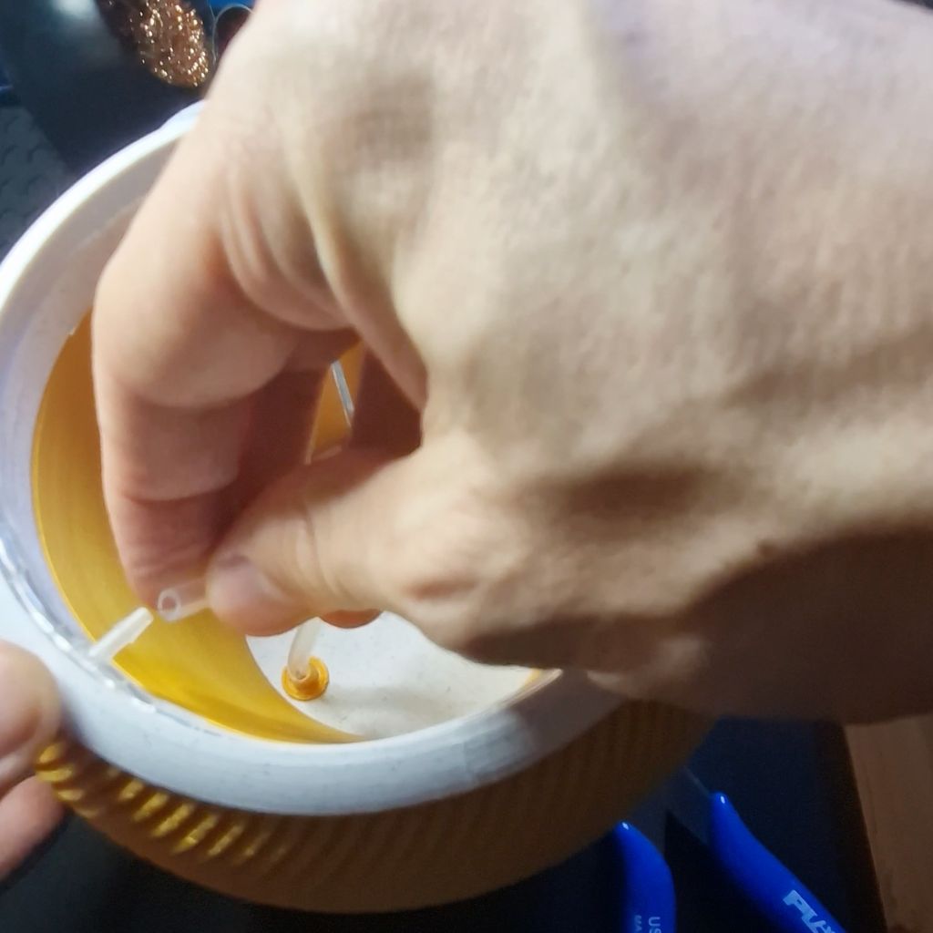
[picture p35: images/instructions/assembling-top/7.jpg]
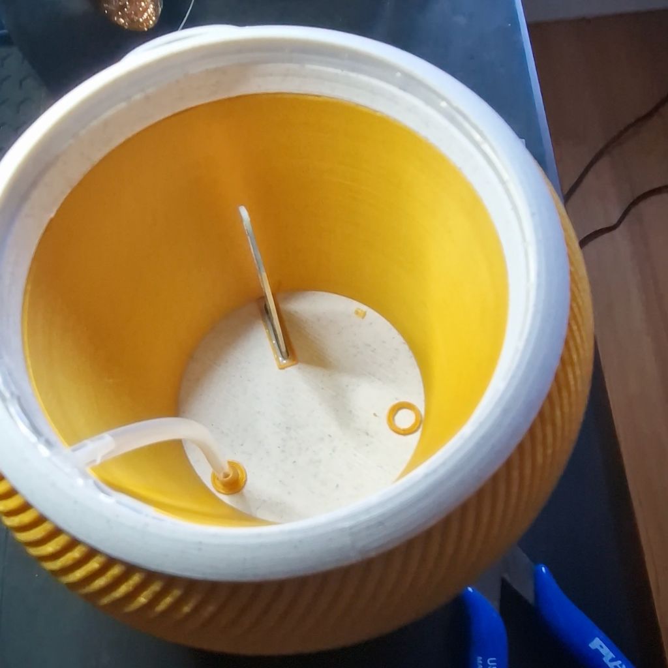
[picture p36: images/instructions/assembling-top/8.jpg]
|  |  |  |  |

<br />**9.** place the sensor protector on the inner planter (it will protect the roots of the plant when you insert it into the vase)
<br />**10.** put your plant into the inner planter
<br />**11.** put the planter into the vase and remove the sensor protector and voilà!

| 9 | 10 | 11 |
| --- | --- | --- |
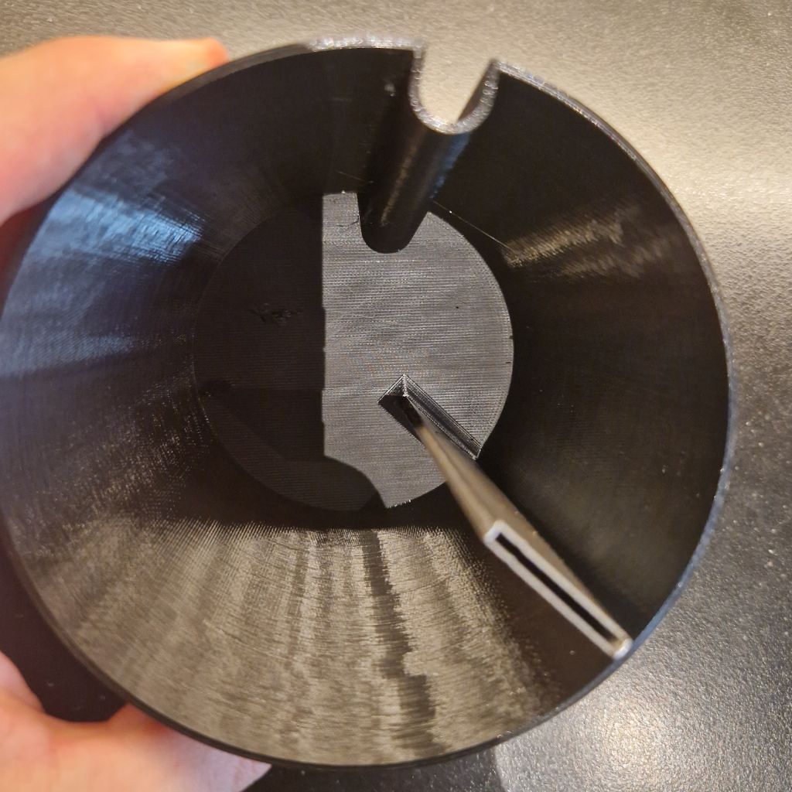
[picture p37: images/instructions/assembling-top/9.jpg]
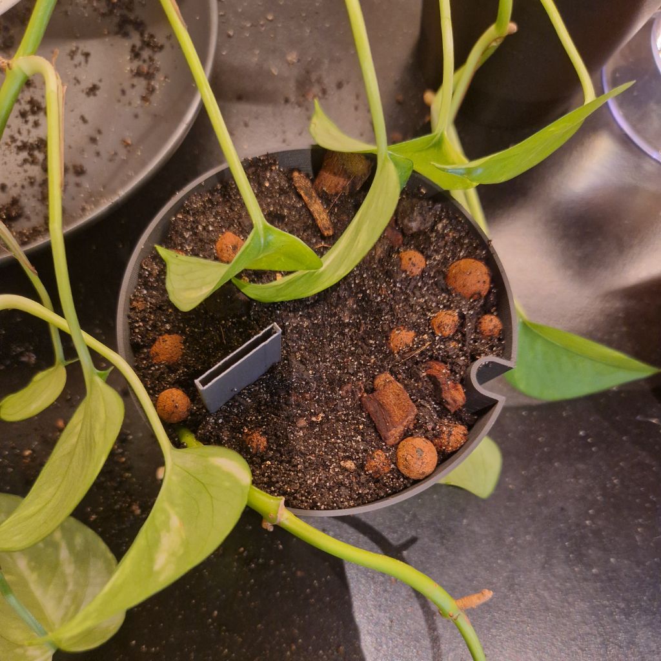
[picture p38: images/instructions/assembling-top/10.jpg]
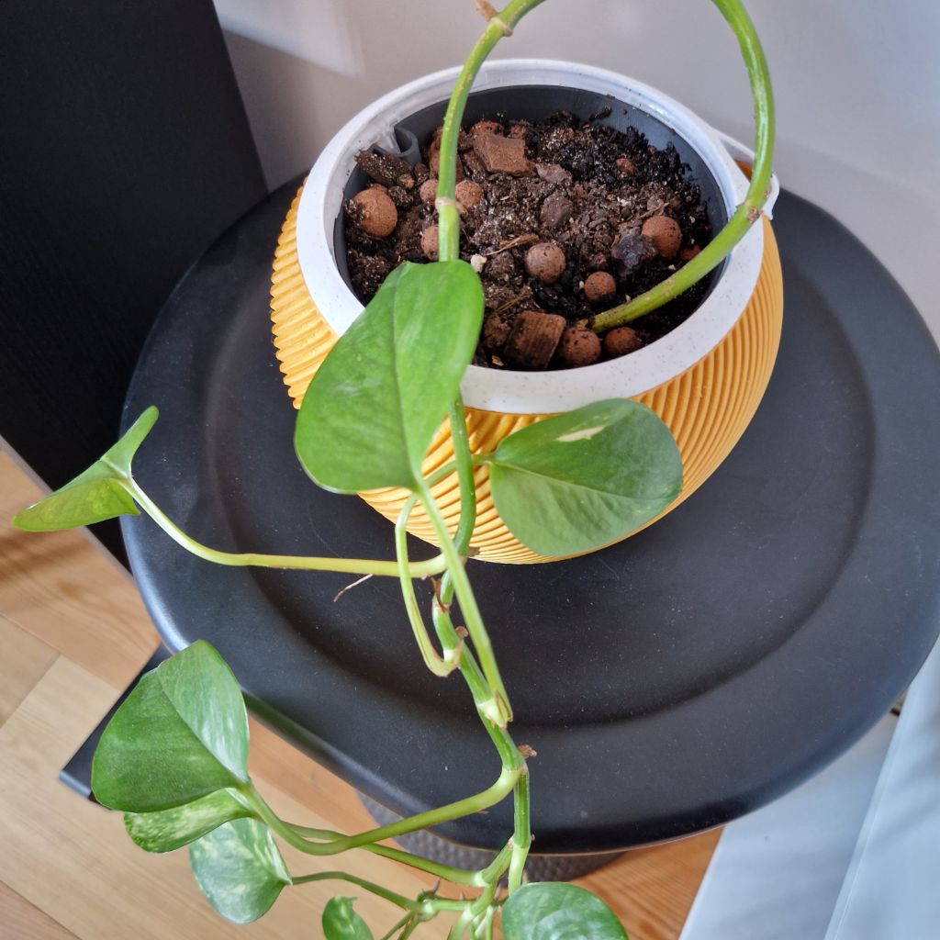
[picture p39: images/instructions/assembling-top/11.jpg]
|  |  |  |

## Home Assistant & ESPHome instructions

### ESPHome only
If you only want to have an autonomous smart plant, you can just upload the ESPHome code to the LolinD32 board by plugging it to your computer. To do that, you need to go to [ESPHome Web](https://web.esphome.io/) and upload the esphome-plantidote.yaml file.

### HomeAssistant & ESPHome
If you want to be able to manually control and monitor your plant, you will need to have a Home Assitant server. For that, [go here](https://www.home-assistant.io/getting-started/).

Once Home Assitant setup, you need to create an ESPHome instance:

- plug your LolinD32 Board to your computer
- go to ESPHome tab on Home Assistant
- click New Device
- whem prompted, choose USB and follow the setup
- once this is finished, click on the top right "secrets" and add the following:

```
wifi_ssid: "yourWifiSsid"
wifi_password: "yourWifiPassword"
ota_password: "otaPasswordYouWant"
```

- click save
- then click Edit to edit yhe code, make sure to copy the api encryption key that is showing up, you will reuse it soon.
- replace the whole content of  the file with the content of esphome-plantidote.yaml and make sure to replace <encryption_key_here> with your key
- click save and install to upload it to the LolinD32 board, do it via USB again.
- once this is done, HA should give you a notification of a new device and you can add it to your integrations.

However, if not detected, you can manually setup a static IP
- edit your entity again and uncomment lines 61 to 64, configure it according to your router
- save and install via USB again.
- go to Home Assistant integrations (Settings > Devices and services), manually add a new integration.
- select ESPHome.
- use your newly set static IP for host, leave the port 6053 as default
- click next, then you will be prompted with the api encryption from earlier

You're all set, you can now configure the dashboard as you like.
See yaml widget files in esphome folder for widget examples.

## Blynk Instructions

[See here](https://github.com/MikeBailleul/plantidote-smart-flower-pot/tree/main/blynk)

## PCB design choices

Most of the component choices were based on the original project.
But I made some changes/improvements.

- I changed the value of the resistor R2 for the MOSFET because according to my calculations, it was not enough. I had the same issues, sometimes triggering, sometimes not, very random. 
- I changed the pin used for the button, it was a strapping pin (pin 0) and it caused me a lot of issues while developing the code so I changed it to another one (pin 13).
- I freed one pin and removed one resistor for reading the battery voltage because I discovered that the LolinD32 has a built-in feature for that
- I connected all LolinD32 pins to the board, this way, we can use other pins to add features if the project evolves more. Because of that I had to make the cutout a bit of a weird rectangular shape.
- I removed one pin for the water level, because I felt I didn't need that many

### Resistors calculations
R1, R3 and R4 are just pulldown resistors, so I chose 100kΩ.

R2 is to limit the current drawn by the MOSFET through the GPIO pins.
Lolin D32 max current per GPIO: 12mA
```R = U/Imax = 3.3/0.012 = 275Ω```
So R2 should at least be 275Ω, I chose R2 330Ω. 

### Pins used
| GPIO | Function |
| --- | --- |
| 5  | Built-in LED |
| 13 | Wakeup deep sleep |
| 19 | Power soil moisture sensor |
| 17 | Power pump |
| 27 | Power water level sensor 100% |
| 26 | Power water level sensor 70% |
| 25 | Power water level sensor 30% |
| 33 | Power water level sensor 10% |
| 32 | Water level sensor signal |
| 34 | Soil moisture sensor signal |
| 35 | Battery voltage |

I avoided the use of strapping pins, on ESP32 they are: 0, 2, 4, 12, 15

## Some Fusion 360 PCB tips

### To edit a single component footprint:

- Go on Schematics
- Find component in "Place component" left panel > right click > Edit library
- Find the footprint and double click will open the footprint editor
- Edit as you need and save
- Go back to schematic, right click the schematic component you wanted to update > replace
- A window opens, click on Open library to enable your custom library
- Find your component in the list

This should update the footprint in the PCB editor

### To check errors before export:

- In schematics > Validate > Errors > Check everything OK then sync
- In PCB editor > Rules DRC/ERC > DRC > Check everything OK

### To export PCB manufacturing files:

- In PCB editor > Manufacturing > CAM processor > CAM
- In output files tab > Gerber > Profile > Add layer > 46 milling
- Process job
- Send files in "DrillFiles" and "GerberFiles" to manufacturer

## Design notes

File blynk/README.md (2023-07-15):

## Blynk Instructions for Plantidote

This code is only useful if you want the vase to work with Blynk.

- Use platform.io to import the blynk folder
- Create myconfig.h file based on myconfig.sample.h
- Compile/upload it to the board
- Create a dashboard on Blynk with the following datastreams:
  - V0: Gauge for the battery voltage
  - V1: Gauge for the battery percentage
  - V2: Graph for the moisture level
  - V3: Gauge for the water level
  - V4: Slider for the moisture threshold
  - V5: Switch for the pump

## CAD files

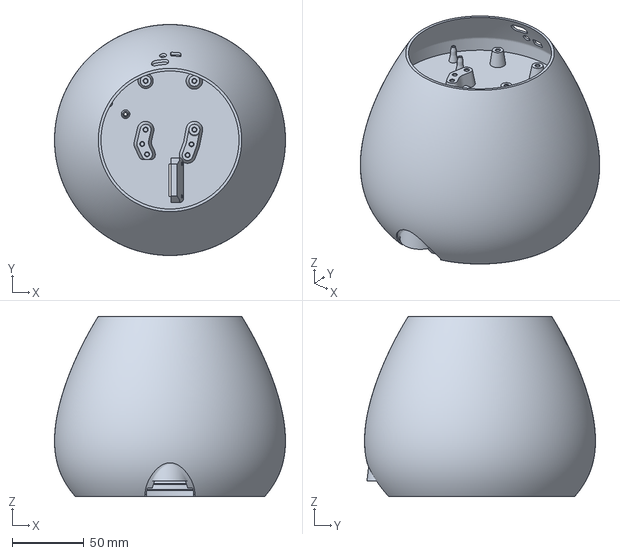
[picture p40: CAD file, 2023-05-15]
hardware/vase/3mf/shells/shell-round.3mf
161.2 x 161.2 x 125.9 mm

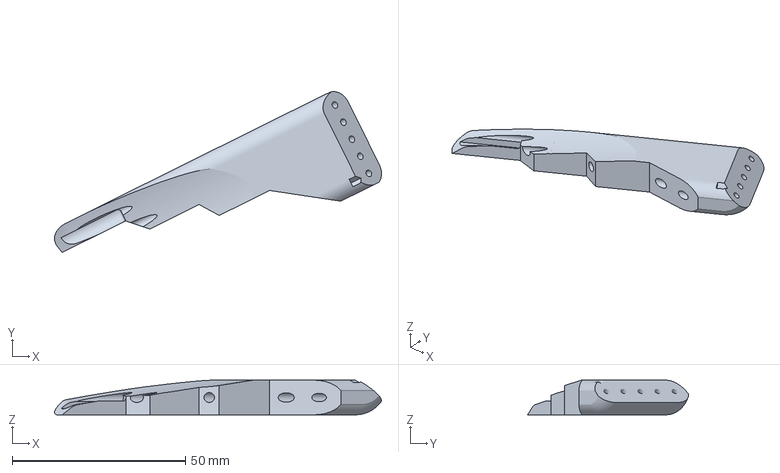
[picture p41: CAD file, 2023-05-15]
hardware/vase/3mf/water-sensor-cable-tester.3mf
94.3 x 46.4 x 10.0 mm

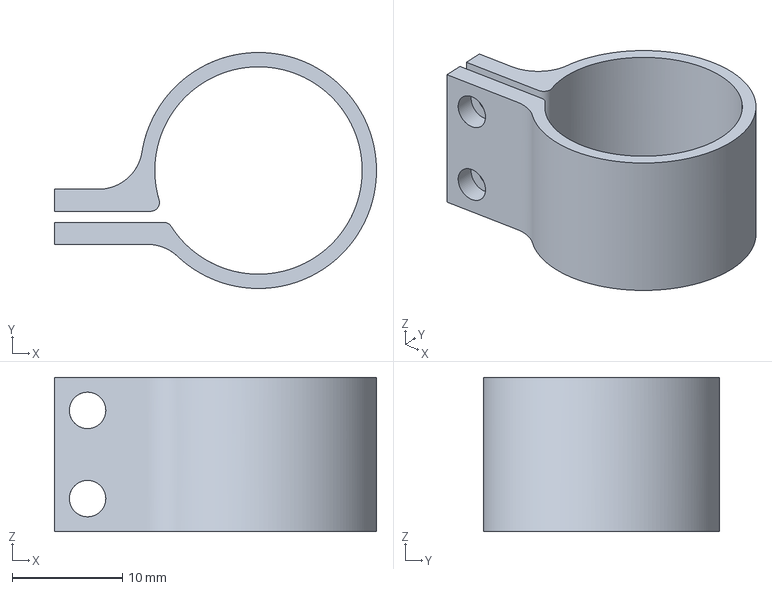
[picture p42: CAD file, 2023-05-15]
hardware/vase/3mf/mount-battery.3mf
29.2 x 21.4 x 14.0 mm

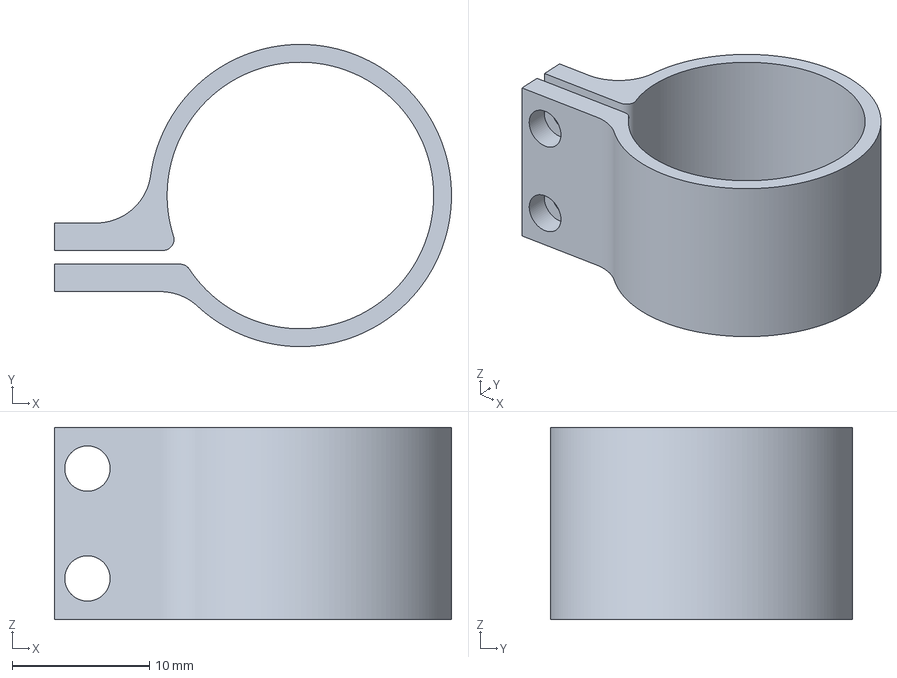
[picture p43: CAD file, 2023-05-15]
hardware/vase/3mf/mount-pump.3mf
28.9 x 22.0 x 14.0 mm

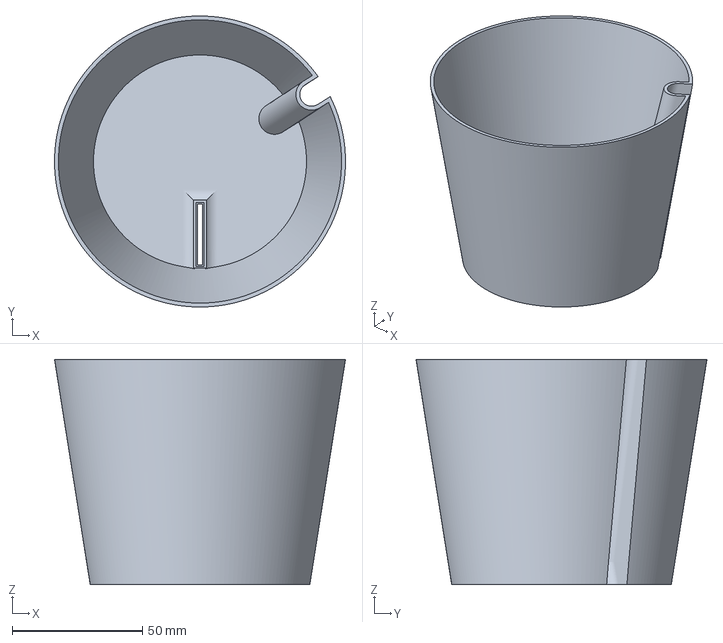
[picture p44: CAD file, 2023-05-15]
hardware/vase/3mf/inner-planter.3mf
111.6 x 111.6 x 86.4 mm

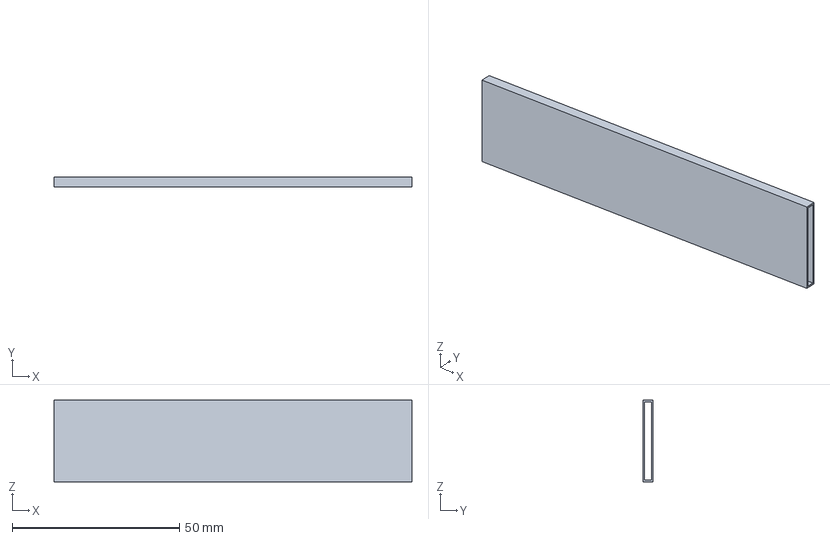
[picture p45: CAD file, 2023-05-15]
hardware/vase/3mf/sensor-protector.3mf
107.0 x 3.00 x 24.4 mm

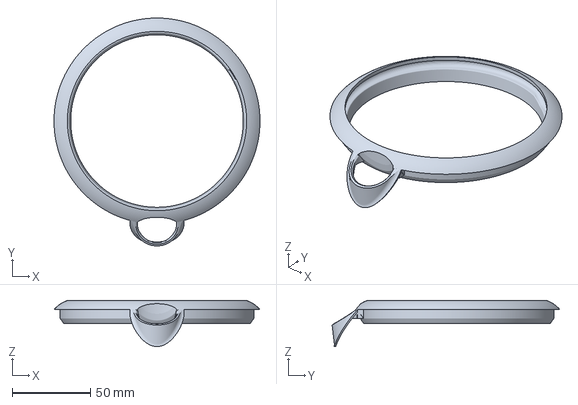
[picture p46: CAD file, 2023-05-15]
hardware/vase/3mf/top-lid.3mf
131.9 x 145.9 x 29.5 mm

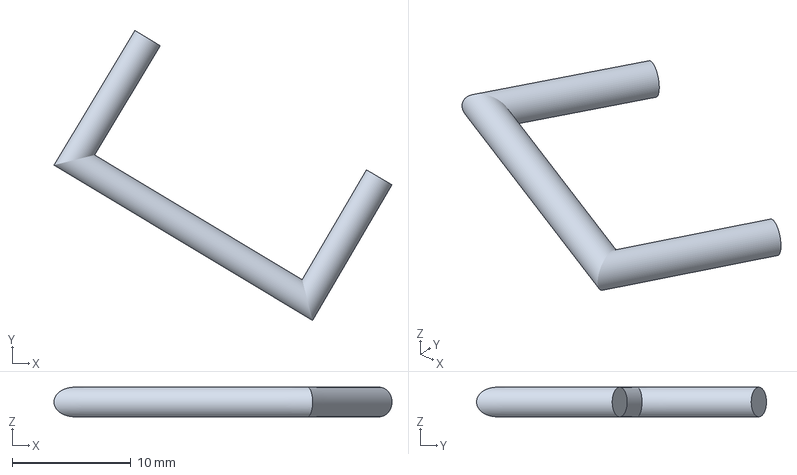
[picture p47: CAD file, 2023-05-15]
hardware/vase/3mf/sensor-holder.3mf
28.5 x 24.5 x 2.50 mm

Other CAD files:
hardware/vase/STL/inner-planter.stl
hardware/vase/STL/mount-battery.stl
hardware/vase/STL/mount-pump.stl
hardware/vase/STL/sensor-holder.stl
hardware/vase/STL/sensor-protector.stl
hardware/vase/STL/top-lid.stl
hardware/vase/STL/water-sensor-cable-tester.stl

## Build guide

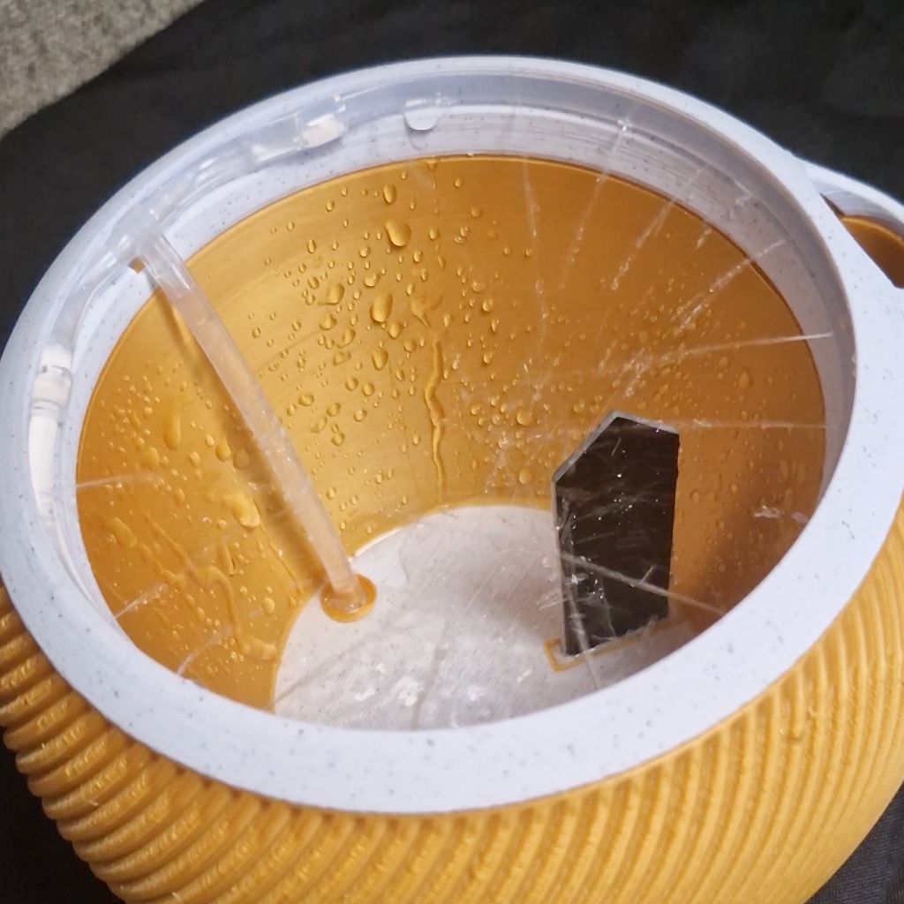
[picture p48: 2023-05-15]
images/instructions/assembling-top/12.jpg

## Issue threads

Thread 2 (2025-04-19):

Deep Sleep doesn't last

fredmccr, 2025-04-19:
Hi,
I noticed that the deep sleep doesn't last for more than a few seconds, leading to a fast discharge of the battery.
I attached a log file (without my credentials), hoping someone could help me to fix that.
Thanks !

[logs_esphome-web-d70b20_logs.txt](https://github.com/user-attachments/files/19821476/logs_esphome-web-d70b20_logs.txt)

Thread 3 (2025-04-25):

What is the water level sensor used ?

vishnusure, 2025-04-25:
How is the water level detected with 6 ends of a cable placed in soil and the other 6 ends connected to board with not conductive probes ?  Is a IC or module not used for measuring the water level using conductive probes ?

MikeBailleul, 2025-05-04:
The water level sensor is just 5 ends of a cable. It's not placed in soil.
See this picture: https://github.com/MikeBailleul/plantidote-smart-flower-pot/blob/main/images/instructions/sealing/6.jpg

No need to buy a water level sensor, those cable are enough because water is conductive. So my code test if there is voltage between 2 cable end, if voltage > 0.1V then there is water, otherwise no water at this level.

vishnusure, 2025-05-04:
Yes I have done in detail through your DIY water sensor and understood how it works . It needs only one ADC pin with a pull up resistor and for remaining levels like 70%, 30% etc .. normal GPIO pins can be used right ?

MikeBailleul, 2025-05-06:
Yes, that's correct!

Closed 2025-05-04.

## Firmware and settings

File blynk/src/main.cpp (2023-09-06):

#include <Arduino.h>
#include <Button/Button.h>
#include <Battery/Battery.h>
#include <Moisture/Moisture.h>
#include <WaterPump/WaterPump.h>
#include <WaterLevel/WaterLevel.h>
#include <myconfig.h>
#include <Preferences.h>

// ------------------------ Blynk import ------------------------ //

#include <WiFi.h>
#include <WiFiClient.h>
#include <BlynkSimpleEsp32.h>


// ------------------------ Bluetooth ------------------------ //

#include "BluetoothSerial.h"

#if !defined(CONFIG_BT_ENABLED) || !defined(CONFIG_BLUEDROID_ENABLED)
#error Bluetooth is not enabled! Please run `make menuconfig` to enable it
#endif

BluetoothSerial SerialBT;
bool clientConnected = false; // Track if a client is connected

#define CREDENTIAL_SEPARATOR "::" // SSID::PASSWORD

// ------------------------ Deep sleep config ---------------------- //

#define WAKEUP_LEVEL  HIGH  // Trigger wakeup when button is HIGH
#define uS_TO_S_FACTOR 1000000LL  // Conversion factor for micro seconds to seconds
#define TIME_TO_SLEEP  86400 * uS_TO_S_FACTOR
#define TIME_TO_SLEEP_FOREVER  31536000 * uS_TO_S_FACTOR

Preferences preferences;

// ------------------------ Pins ---------------------- //

const gpio_num_t PIN_BUTTON = GPIO_NUM_13;

const gpio_num_t PIN_PUMP_POWER = GPIO_NUM_17;
const uint16_t PUMP_DURATION = 5000;

const gpio_num_t PIN_MOISTURE_POWER = GPIO_NUM_19;
const gpio_num_t PIN_MOISTURE_SIGNAL = GPIO_NUM_34;
const uint16_t MOISTURE_CALIBRATION_WATER = 821; // hardcoded for now, TODO claibrate directly from app
const uint16_t MOISTURE_CALIBRATION_AIR = 2535; // hardcoded for now, TODO claibrate directly from app

const gpio_num_t PIN_WATER_POWER_LEVEL_100 = GPIO_NUM_27;
const gpio_num_t PIN_WATER_POWER_LEVEL_70 = GPIO_NUM_26;
const gpio_num_t PIN_WATER_POWER_LEVEL_30 = GPIO_NUM_25;
const gpio_num_t PIN_WATER_POWER_LEVEL_10 = GPIO_NUM_33;
const gpio_num_t PIN_WATER_SIGNAL = GPIO_NUM_32;

const gpio_num_t PIN_BATTERY_LEVEL = GPIO_NUM_35;
const float BATTERY_MIN_VOLTAGE = 3.3;
const float BATTERY_MAX_VOLTAGE = 4.2;
const float BATTERY_THRESHOLD = 3.4;

const gpio_num_t PIN_BUILTIN_LED = GPIO_NUM_5;

// ------------------------ Constants ---------------------- //

const uint16_t MEASURE_WAITING_TIME = 250; // time to wait between measurements

// ------------------------ Cycle controller ---------------------- //

const uint16_t LOOP_FREQUENCY = 25; // Hz
const uint16_t WAIT_PERIOD = 1000 / LOOP_FREQUENCY; // ms
struct Timer {
    uint32_t laptime;
    uint32_t ticks;
};
Timer cycleTimer;
BlynkTimer pumpTimer;
BlynkTimer hibernationTimer;

// ------------------------ Declarations ---------------------- //
Button button(PIN_BUTTON);
WaterPump waterPump(PIN_PUMP_POWER, PUMP_DURATION);
Moisture moisture(PIN_MOISTURE_POWER, PIN_MOISTURE_SIGNAL, MEASURE_WAITING_TIME, MOISTURE_CALIBRATION_WATER, MOISTURE_CALIBRATION_AIR);
Battery battery(PIN_BATTERY_LEVEL, MEASURE_WAITING_TIME, BATTERY_MIN_VOLTAGE, BATTERY_MAX_VOLTAGE);
WaterLevel waterLevel(PIN_WATER_SIGNAL, PIN_WATER_POWER_LEVEL_10, PIN_WATER_POWER_LEVEL_30, PIN_WATER_POWER_LEVEL_70, PIN_WATER_POWER_LEVEL_100, MEASURE_WAITING_TIME);

int8_t moistureThreshold = 50;

// ------------------------ Blynk Config ---------------------- //

// called every time the device is connected to Blynk.Cloud
BLYNK_CONNECTED() {
}

// called every time the V4 state changes
BLYNK_WRITE(V4) {
    int v4Value = param.asInt();

    if (v4Value < 0) {
        moistureThreshold = 0;
    } else if (v4Value > 100) {
        moistureThreshold = 100;
    } else {
        moistureThreshold = v4Value;
    }

    Serial.println("V4 received, moisture threshold: " + String(moistureThreshold));
}

void turnOffBlynkPumpSwitch() {
    Blynk.virtualWrite(V5, 0);
}

// called every time the V5 state changes
BLYNK_WRITE(V5) {
    int v5Value = param.asInt();

    if (v5Value == 1) {
        waterPump.startPumping();
        Blynk.virtualWrite(V6, 1); // log pump action
        pumpTimer.setTimeout(PUMP_DURATION, turnOffBlynkPumpSwitch);
    } else {
        waterPump.stopPumping();
    }

    Serial.println("V5 received, switch pumping ON/OFF: " + String(v5Value));
}

void sendDataToBlynk() {
    Serial.println("Sending data to Blynk");

    Serial.println("Battery voltage: "+ String(battery.getBatteryVoltage()));
    Serial.println("Battery percentage: "+ String(battery.getBatteryPercentage()));
    Serial.println("Moisture level: "+ String(moisture.getMoisturePercentage()));
    Serial.println("Water level: "+ String(waterLevel.getWaterPercentage()));

    Blynk.virtualWrite(V0, battery.getBatteryVoltage());
    Blynk.virtualWrite(V1, battery.getBatteryPercentage());
    Blynk.virtualWrite(V2, moisture.getMoisturePercentage());
    Blynk.virtualWrite(V3, waterLevel.getWaterPercentage());
}

// ------------------------ Deep sleep functions ---------------------- //

void deepSleep(long long int timeToSleep) {
    esp_sleep_enable_ext0_wakeup((gpio_num_t)PIN_BUTTON, WAKEUP_LEVEL);
    esp_sleep_enable_timer_wakeup(timeToSleep);
    esp_deep_sleep_start();
}


void hibernate() {
    Serial.println("--- ZZZZZzzzzz ---");

    esp_sleep_pd_config(ESP_PD_DOMAIN_RTC_SLOW_MEM, ESP_PD_OPTION_OFF);
    esp_sleep_pd_config(ESP_PD_DOMAIN_RTC_FAST_MEM, ESP_PD_OPTION_OFF);
    esp_sleep_pd_config(ESP_PD_DOMAIN_XTAL,         ESP_PD_OPTION_OFF);
    deepSleep(TIME_TO_SLEEP);
}

void sleepForeverIfNeeded() {
    if (battery.getBatteryVoltage() <= BATTERY_THRESHOLD) {
        Blynk.virtualWrite(V7, 0);
        Serial.println("--- Sleep forever because battery is lower than safety threshold ---");

        esp_sleep_pd_config(ESP_PD_DOMAIN_RTC_SLOW_MEM, ESP_PD_OPTION_OFF);
        esp_sleep_pd_config(ESP_PD_DOMAIN_RTC_FAST_MEM, ESP_PD_OPTION_OFF);
        esp_sleep_pd_config(ESP_PD_DOMAIN_XTAL,         ESP_PD_OPTION_OFF);

        deepSleep(TIME_TO_SLEEP_FOREVER);
    } else {
        Serial.println("--- Battery health OK: " + String(battery.getBatteryVoltage()) + "V ---");
    }
}

void prepareForHibernation() {
    if (esp_sleep_get_wakeup_cause() == ESP_SLEEP_WAKEUP_EXT0) {
        // was woken up by user action
        // maybe user wants to do something
        // let's not go to sleep immediately
        Serial.println("--- Going to sleep in 1 min ---");
        hibernationTimer.setTimeout(60000L, hibernate);
    } else {
        Serial.println("--- Going to sleep in 10s ---");
        hibernationTimer.setTimeout(10000L, hibernate);
    }
}

// ------------------------ Storage preferences functions ---------------------- //

void clearWifiCredentials() {
    preferences.begin("wifi", false); // Use the same namespace that you used for these preferences
    preferences.remove("ssid");
    preferences.remove("password");
    preferences.end();
}

void saveCredentials(const String &ssid, const String &password) {
    preferences.begin("wifi", false);
    preferences.putString("ssid", ssid);
    preferences.putString("password", password);
    preferences.end();
}

void loadCredentials(char* ssid, char* password) {
    preferences.begin("wifi", false);
    String ssidStr = preferences.getString("ssid", WIFI_SSID); // load from config if empty
    String passwordStr = preferences.getString("password", WIFI_PASSWORD); // load from config if empty
    preferences.end();

    // load the strings into the char*
    ssidStr.toCharArray(ssid, ssidStr.length() + 1);
    passwordStr.toCharArray(password, passwordStr.length() + 1);
}

// ------------------------ Bluetooth functions ---------------------- //

void handleBTWelcomeMessage() {
    SerialBT.println("Hello " + String(USERNAME) + "!");
    SerialBT.println("Enter your Wifi credentials separated by ::");
    SerialBT.println("MyWifi::MyWonderfulPassword");
}

void handleBTWifiCredentials(String receivedData) {
    int separatorIndex = receivedData.indexOf(CREDENTIAL_SEPARATOR);
    String ssid = receivedData.substring(0, separatorIndex);
    String password = receivedData.substring(separatorIndex + strlen(CREDENTIAL_SEPARATOR));

    saveCredentials(ssid, password);

    SerialBT.println("Connecting to " + ssid + " with password: " + password);
    SerialBT.println("Check Blynk app");

    WiFi.begin(ssid, password);
    // ESP.restart();
}

void listenForBluetoothInteractions() {
    if (SerialBT.hasClient()) {
        String receivedData = SerialBT.readStringUntil('\n');
        receivedData.trim(); 

        if (!clientConnected || receivedData.equalsIgnoreCase("hello") || receivedData.equalsIgnoreCase("hi")) {
            handleBTWelcomeMessage();
            clientConnected = true;
        } else if (receivedData.indexOf(CREDENTIAL_SEPARATOR) != -1) {
            handleBTWifiCredentials(receivedData);
        }
    } else {
        clientConnected = false;
    }
}

// ------------------------ Methods ---------------------- //

void waitForNextCycle() {
    uint32_t now;
    do { now = millis(); } while (now - cycleTimer.laptime < WAIT_PERIOD);
    cycleTimer.laptime = now;
    cycleTimer.ticks++;
}

void startMeasures() {
    Serial.println("--- Measuring start ---");
    battery.startMeasure();
    moisture.startMeasure();
    waterLevel.startMesure();
}

bool isMeasuringCompleted() {
    return battery.getBatteryVoltage() != -1
        && moisture.getMoisturePercentage() != -1
        && waterLevel.getWaterPercentage() != -1;
}

void waterPlantIfNeeded() {
    Serial.println("--- Moisture " + String(moisture.getMoisturePercentage()) + "% --- threshold: " + moistureThreshold + "% ---");
    if (waterLevel.getWaterPercentage() > 0 && moisture.getMoisturePercentage() < moistureThreshold) {
        Serial.println("--- Watering thirsty plant --");
        waterPump.startPumping();
        Blynk.virtualWrite(V6, 1); // log pump action
    } else {
        Serial.println("--- No need to water plant --");
    }
}

// ------------------------ Core ---------------------- //

bool needToStartMeasure = true;
bool needToSendDataBlynk = true;
bool needToCheckWatering = true;
bool needToCheckBatteryHealth = true;

void startTasks() {
    if (needToStartMeasure) {
        needToStartMeasure = false;
        startMeasures();
    }

    if (isMeasuringCompleted()) {
        if (needToCheckBatteryHealth) {
            needToCheckBatteryHealth = false;
            sleepForeverIfNeeded();
        }

        if (needToCheckWatering) {
            needToCheckWatering = false;
            waterPlantIfNeeded();
        }
        

        if (needToSendDataBlynk) {
            needToSendDataBlynk = false;
            sendDataToBlynk();
            prepareForHibernation();
        }   
    }
}

void setup() {
    Serial.begin(115200);

    if (esp_sleep_get_wakeup_cause() == ESP_SLEEP_WAKEUP_EXT0) {
        // need to be woken by user action to enable bluetooth configuration
        SerialBT.begin("Plantidote");
    }

    pinMode(PIN_BUILTIN_LED, OUTPUT);
    digitalWrite(PIN_BUILTIN_LED, LOW);

    char ssid[32];
    char password[32];

    loadCredentials(ssid, password);

    WiFi.begin(ssid, password);
    Blynk.config(BLYNK_AUTH_TOKEN); // Configure Blynk to use WiFi, but don't connect yet
    Blynk.syncVirtual(V4);
}

void loop() {
    if (WiFi.status() == WL_CONNECTED) {
        // Only try to connect Blynk if WiFi is connected
        if (!Blynk.connected()) {
            Blynk.connect();
        }
    }

    Blynk.run();
    pumpTimer.run();
    hibernationTimer.run();

    button.loopRoutine();
    battery.loopRoutine();
    moisture.loopRoutine();
    waterPump.loopRoutine();
    waterLevel.loopRoutine();

    startTasks();
    listenForBluetoothInteractions();

    waitForNextCycle();
}

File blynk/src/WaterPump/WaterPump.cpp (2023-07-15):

#include "WaterPump.h"

// -------------------------------- private methods -------------------------------- //

void WaterPump::goToState(WaterPumpState newState) {
    state = newState % IDLE;
    // Serial.println("Force new pump state: " + String(state));
}

void WaterPump::goToNextState() {
    state = (state + 1) % IDLE;
    // Serial.println("Go to next water pump state: " + String(state));
}

void WaterPump::initState() {
    pumpOperationStartTime = millis();
    goToNextState();
}

void WaterPump::pumpRunState() {
    if (millis() - pumpOperationStartTime < pumpOperationDuration) {
        digitalWrite(pin, HIGH);
    } else {
        goToNextState();
    }
}

void WaterPump::pumpStopState() {
    digitalWrite(pin, LOW);
    goToNextState();
}

bool WaterPump::isIdle() {
    return state % IDLE == 0;
}

// -------------------------------- public methods -------------------------------- //

WaterPump::WaterPump(gpio_num_t pin, unsigned long pumpOperationDuration) {
    WaterPump::pin = pin;
    WaterPump::pumpOperationDuration = pumpOperationDuration;
    pinMode(pin, OUTPUT);
}

void WaterPump::loopRoutine() {
    switch (state) {
    case IDLE:
        break;

    case INITIALIZING:
        initState();

    case PUMPING:
        pumpRunState();
        break;

    case STOPPING:
        pumpStopState();
        break;
    
    default:
        break;
    }
}

void WaterPump::startPumping() {
    if (isIdle()) {
        goToNextState();
    } else {
        Serial.println("Pump not IDLE, already in state: " + String(state));
    }
}

void WaterPump::stopPumping() {
    if (!isIdle()) {
        goToState(STOPPING);
    } else {
        Serial.println("Pump already IDLE");
    }
}

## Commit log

2022-09-19 Add button press and battery percentage reading
2022-09-20 Add water pump
2022-09-20 Add water level sensor
2022-09-20 Fix battery bug
2022-09-20 Add soil moisture sensor
2022-10-09 Use pull down resistor on PCB, no need for pullup anymore
2022-10-09 Update pins with new PCB
2023-05-08 Add components and gerber files
2023-05-15 Add stl and 3mf files
    [inner-planter.3mf, inner-planter.stl, mount-battery.3mf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]
2023-05-16 Update link PCB
2023-05-18 Update readme with pcb design choices
2023-07-15 Simplify battery reading in blynk
2023-07-15 Update water level sensor reading in blynk
2023-07-15 Add health battery check to blynk
2023-07-18 Use highest of 10 measures for water level sensor blynk
2023-09-06 Fix bug battery for blynk
    [Battery.cpp, main.cpp]
2026-02-05 Update stl and add step files
